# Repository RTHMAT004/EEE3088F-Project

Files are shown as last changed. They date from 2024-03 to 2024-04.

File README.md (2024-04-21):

# EEE3088F-Project
Power and Sensing repository for the EEE3088F Project. Group 24: RTHMAT004 and CLRMAT005

This repository contains files for both the sensing and power subsystems of a Micromouse for a university project. This project involved developing a Micromouse, therefore these solutions are built with existing systems in mind (microcontroller, servo motors etc). 

The power system deals with powering the two motors of the Micromouse, managing the charging of the battery and turning the Micromouse on and off.

The sensing system deals with surface detection around the Micromouse, inevitabely helping the micromouse navigate. The sensor does not make decisions of movement, or deal with any power control, it's only purpose is to detect objects and returning results using a voltage output signal. 

# Sensing subsystem:
The folder named "SensorKiCad-RTHMAT004" contains the KiCad files for the sensor subsystem. This subsystem solves the problem of sensing for the micromouse. This subsystem uses IR frequencies to detect objects within the bounds of the sensor. This subsystem solution should be used as a springboard for ideas surrounding sensing for devices such as a micromouse.  

# Power Subsytem
The folder named "PowerKiCad-CLRMAT005" contains the KiCad files for the power subsystem. This subsystem manages everything involving the powering of the Micromouse. This subsystem uses integrated circuits to control the motors and charging of the mouse. This subsystem solution should be used as a springboard for ideas surrounding the powering of small robotics.

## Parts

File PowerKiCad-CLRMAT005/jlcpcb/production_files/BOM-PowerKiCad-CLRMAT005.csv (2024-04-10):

Comment | Designator | Footprint | LCSC
0.1uF | C1,C2 | C_0603_1608Metric | C14663
1.2k | R3 | R_0805_2012Metric | C17379
470 | R2 | R_0805_2012Metric | C17710
4.7uF | C3,C4 | C_0805_2012Metric | C1779
SW_SPDT | SW1 | SW_Lever_1P2T_NKK_GW12LxH | C1788490
LED | D1 | LED_0603_1608Metric | C2286
LEFT MOTOR | U1,U2 | WSON-8-1EP_2x2mm_P0.5mm_EP0.9x1.6mm | C39159
2k | R1 | R_0402_1005Metric | C4109
3k | R4 | R_0603_1608Metric | C4211
MCP73831-2-OT | U3 | SOT-23-5 | C424093
Conn_01x02_Pin | J2 | JST_PH_B2B-PH-K_1x02_P2.00mm_Vertical
Conn_01x16_Pin | J1 | PinSocket_2x08_P2.54mm_Vertical

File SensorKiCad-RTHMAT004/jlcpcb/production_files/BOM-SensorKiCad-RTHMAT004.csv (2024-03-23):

Comment | Designator | Footprint | LCSC
BPV22NF | D10,D2,D3,D4 | XDCR_BPV22NF | C130226
47 | R1,R10,R12,R15,R17,R2,R20,R22,R25,R27,R30,R43,R47,R51,R55,R7 | R_0805_2012Metric | C17714
8.2k | R13,R18,R23,R28,R4,R40,R44,R48,R52,R8 | R_0805_2012Metric | C17828
100 | R11,R16,R21,R26,R3,R31,R32,R33,R34,R36,R38,R42,R46,R50,R54,R6 | R_0805_2012Metric | C17901
10k | R14,R19,R24,R29,R41,R5,R53,R9 | R_1206_3216Metric | C17902
SS8050 | Q1,Q2,Q3,Q4,Q5,Q6,Q7 | SOT-23 | C2150
SFH_4544 | D1,D5,D6,D7,D8,D9 | LED_D5.0mm_Horizontal_O1.27mm_Z3.0mm_IRBlack_JLCPCB | C2900370
1k | R35,R37,R39 | R_1206_3216Metric | C4410

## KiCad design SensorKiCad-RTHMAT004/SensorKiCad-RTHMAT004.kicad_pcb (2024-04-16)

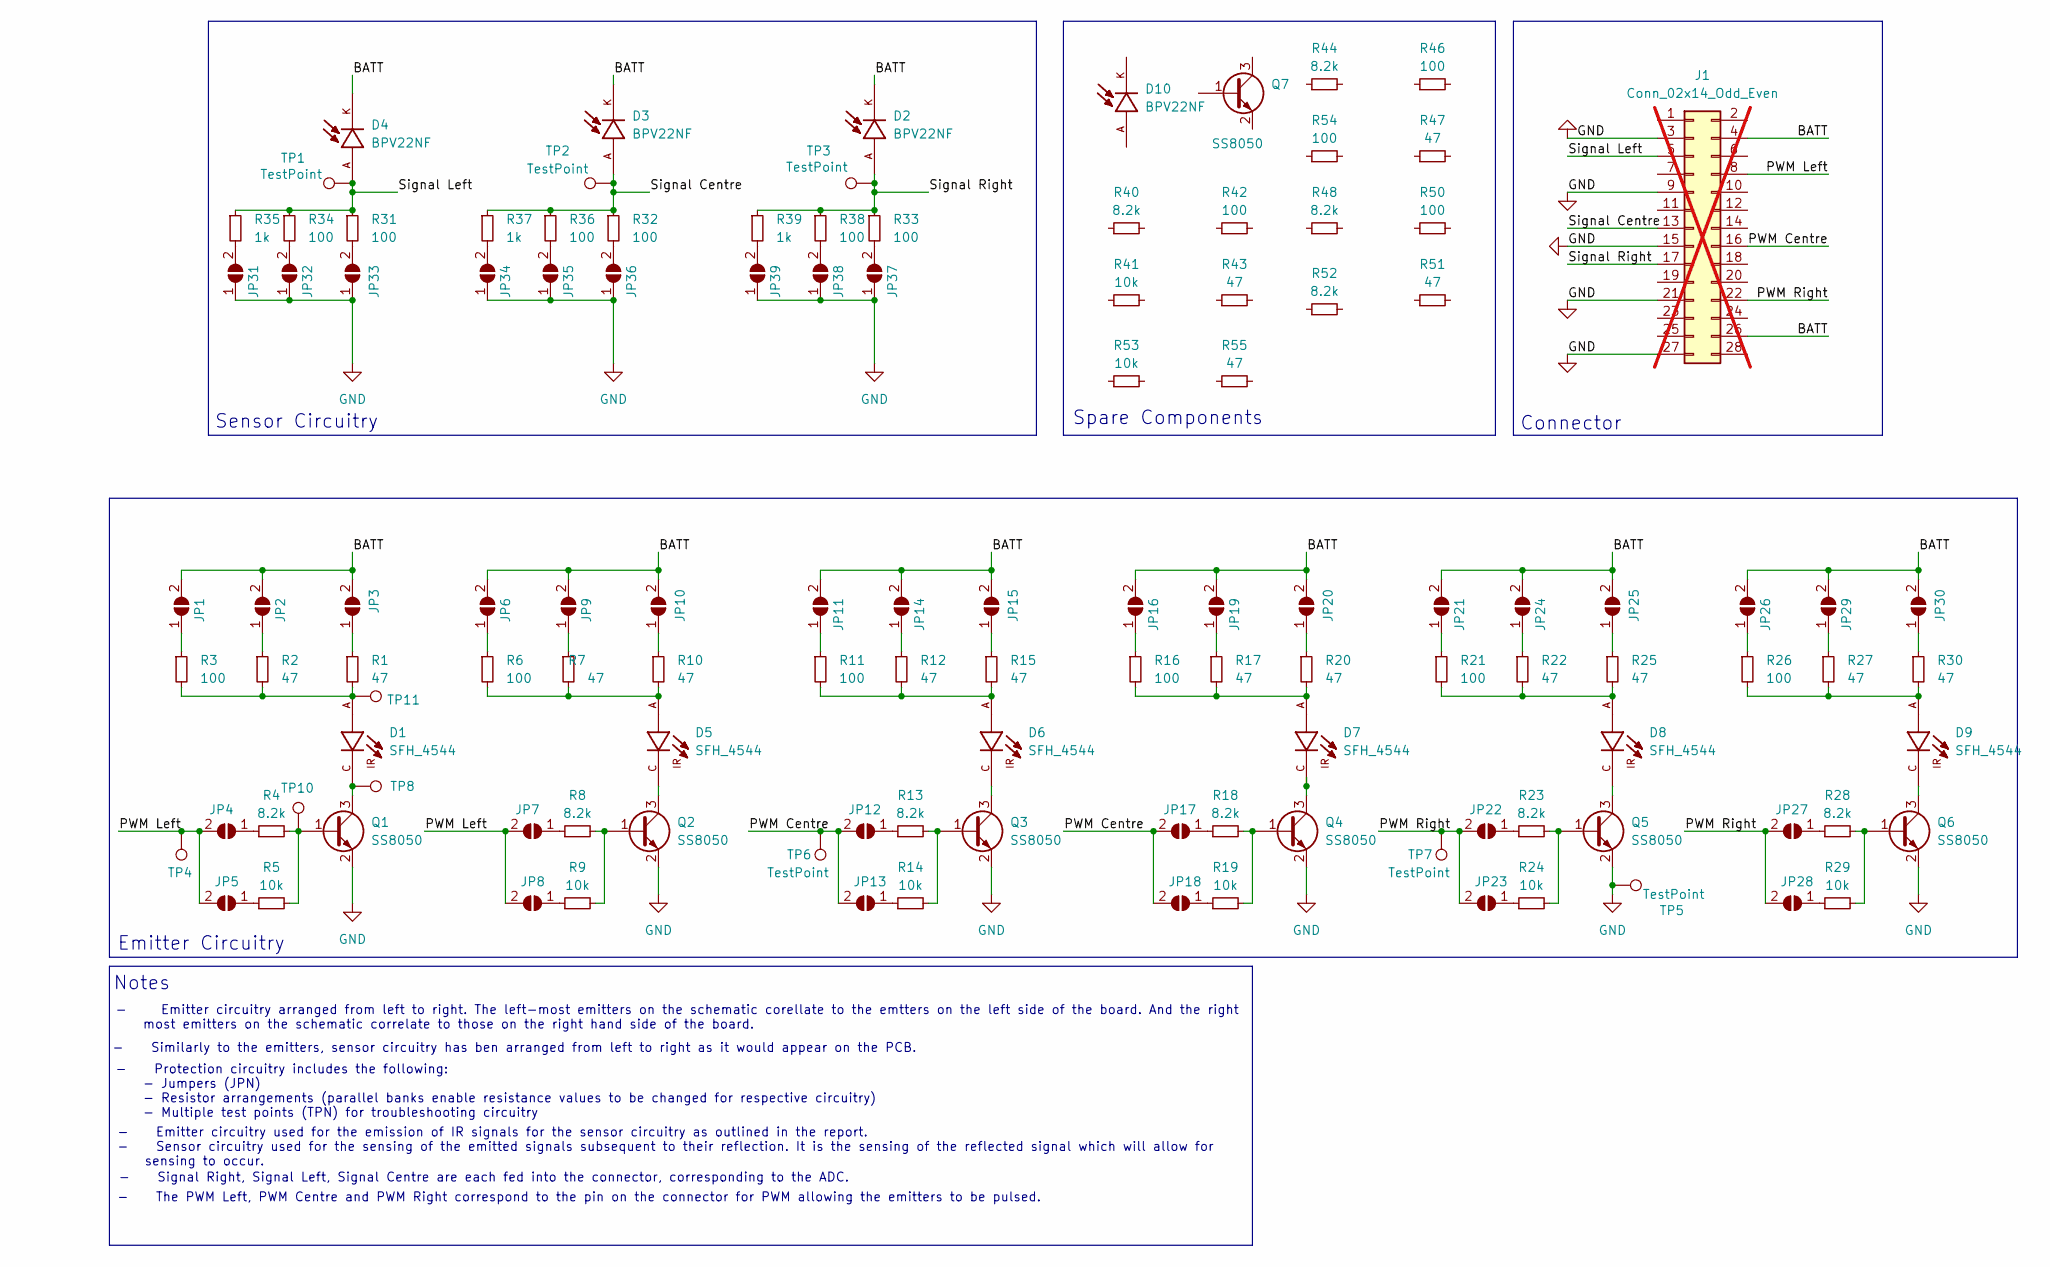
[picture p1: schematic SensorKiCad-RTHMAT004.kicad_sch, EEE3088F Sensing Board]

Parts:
D1, D5, D6, D7, D8, D9: SFH_4544; LED_D5.0mm_Horizontal_O1.27mm_Z3.0mm_IRBlack_JLCPCB; PARTREV 1.3; LCSC C2900370
D2, D3, D4, D10: BPV22NF; XDCR_BPV22NF; PARTREV 1.9; LCSC C130226
J1: Conn_02x14_Odd_Even; PinHeader_2x14_P2.54mm_Vertical; not fitted
JP1, JP2, JP3, JP4, JP5, JP6, JP7, JP8, JP9, JP10, JP11, JP12, JP13, JP14, JP15, JP16, JP17, JP18, JP19, JP20, JP21, JP22, JP23, JP24, JP25, JP26, JP27, JP28, JP29, JP30, JP31, JP32, JP33, JP34, JP35, JP36, JP37, JP38, JP39: SolderJumper_2_Open; SolderJumper-2_P1.3mm_Open_Pad1.0x1.5mm
Q1, Q2, Q3, Q4, Q5, Q6, Q7: SS8050; SOT-23; LCSC C2150
R1, R2, R7, R10, R12, R15, R17, R20, R22, R25, R27, R30, R43, R47, R51, R55: 47; R_0805_2012Metric; LCSC C17714
R3, R6, R11, R16, R21, R26, R31, R32, R33, R34, R36, R38, R42, R46, R50, R54: 100; R_0805_2012Metric; LCSC C17901
R4, R8, R13, R18, R23, R28, R40, R44, R48, R52: 8.2k; R_0805_2012Metric; LCSC C17828
R5, R9, R14, R19, R24, R29, R41, R53: 10k; R_1206_3216Metric; LCSC C17902
R35, R37, R39: 1k; R_1206_3216Metric; LCSC C4410
TP1, TP2, TP3, TP4, TP5, TP6, TP7, TP8, TP10, TP11: TestPoint; TestPoint_Pad_D2.5mm

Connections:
/3V3: J1.2
/BATT: D2.K, D3.K, D4.K, J1.4, J1.26, JP1.2 (B), JP2.2 (B), JP3.2 (B), JP6.2 (B), JP9.2 (B), JP10.2 (B), JP11.2 (B), JP14.2 (B), JP15.2 (B), JP16.2 (B), JP19.2 (B), JP20.2 (B), JP21.2 (B), JP24.2 (B), JP25.2 (B), JP26.2 (B), JP29.2 (B), JP30.2 (B)
/PWM Centre: J1.16, JP12.2 (B), JP13.2 (B), JP17.2 (B), JP18.2 (B), TP6.1
/PWM Left: J1.8, JP4.2 (B), JP5.2 (B), JP7.2 (B), JP8.2 (B), TP4.1
/PWM Right: J1.22, JP22.2 (B), JP23.2 (B), JP27.2 (B), JP28.2 (B), TP7.1
/Signal Centre: D3.A, J1.13, R32.1, R36.1, R37.1, TP2.1
/Signal Left: D4.A, J1.5, R31.1, R34.1, R35.1, TP1.1
/Signal Right: D2.A, J1.17, R33.1, R38.1, R39.1, TP3.1
GND: J1.3, J1.9, J1.15, J1.21, J1.27, JP31.1 (A), JP32.1 (A), JP33.1 (A), JP34.1 (A), JP35.1 (A), JP36.1 (A), JP37.1 (A), JP38.1 (A), JP39.1 (A), Q1.2 (E), Q2.2 (E), Q3.2 (E), Q4.2 (E), Q5.2 (E), Q6.2 (E), TP5.1
unnamed: D1.A, R1.2, R2.2, R3.2, TP11.1
unnamed: D5.A, R6.2, R7.2, R10.2
unnamed: D6.A, R11.2, R12.2, R15.2
unnamed: D7.A, R16.2, R17.2, R20.2
unnamed: D8.A, R21.2, R22.2, R25.2
unnamed: D9.A, R26.2, R27.2, R30.2
unnamed: JP1.1 (A), R3.1
unnamed: JP2.1 (A), R2.1
unnamed: JP3.1 (A), R1.1
unnamed: JP4.1 (A), R4.1
unnamed: JP5.1 (A), R5.1
unnamed: JP6.1 (A), R6.1
unnamed: JP7.1 (A), R8.1
unnamed: JP8.1 (A), R9.1
unnamed: JP9.1 (A), R7.1
unnamed: JP10.1 (A), R10.1
unnamed: JP11.1 (A), R11.1
unnamed: JP12.1 (A), R13.1
unnamed: JP13.1 (A), R14.1
unnamed: JP14.1 (A), R12.1
unnamed: JP15.1 (A), R15.1
unnamed: JP16.1 (A), R16.1
unnamed: JP17.1 (A), R18.1
unnamed: JP18.1 (A), R19.1
unnamed: JP19.1 (A), R17.1
unnamed: JP20.1 (A), R20.1
unnamed: JP21.1 (A), R21.1
unnamed: JP22.1 (A), R23.1
unnamed: JP23.1 (A), R24.1
unnamed: JP24.1 (A), R22.1
unnamed: JP25.1 (A), R25.1
unnamed: JP26.1 (A), R26.1
unnamed: JP27.1 (A), R28.1
unnamed: JP28.1 (A), R29.1
unnamed: JP29.1 (A), R27.1
unnamed: JP30.1 (A), R30.1
unnamed: JP31.2 (B), R35.2
unnamed: JP32.2 (B), R34.2
unnamed: JP33.2 (B), R31.2
unnamed: JP34.2 (B), R37.2
unnamed: JP35.2 (B), R36.2
unnamed: JP36.2 (B), R32.2
unnamed: JP37.2 (B), R33.2
unnamed: JP38.2 (B), R38.2
unnamed: JP39.2 (B), R39.2
unnamed: Q1.1 (B), R4.2, R5.2, TP10.1
unnamed: D1.C, Q1.3 (C), TP8.1
unnamed: Q2.1 (B), R8.2, R9.2
unnamed: D5.C, Q2.3 (C)
unnamed: Q3.1 (B), R13.2, R14.2
unnamed: D6.C, Q3.3 (C)
unnamed: Q4.1 (B), R18.2, R19.2
unnamed: D7.C, Q4.3 (C)
unnamed: Q5.1 (B), R23.2, R24.2
unnamed: D8.C, Q5.3 (C)
unnamed: Q6.1 (B), R28.2, R29.2
unnamed: D9.C, Q6.3 (C)

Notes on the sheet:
- Protection circuitry includes the following: - Jumpers (JPN) - Resistor arrangements (parallel banks enable resistance values to be changed for respective circuitry) - Multiple test points (TPN) for troubleshooting circuitry
Spare Components
Notes
- Emitter circuitry arranged from left to right. The left-most emitters on the schematic corellate to the emtters on the left side of the board. And the right most emitters on the schematic correlate to those on the right hand side of the board.
Emitter Circuitry
- Emitter circuitry used for the emission of IR signals for the sensor circuitry as outlined in the report. - Sensor circuitry used for the sensing of the emitted signals subsequent to their reflection. It is the sensing of the reflected signal which will allow for sensing to occur.
Sensor Circuitry
- The PWM Left, PWM Centre and PWM Right correspond to the pin on the connector for PWM allowing the emitters to be pulsed.
- Similarly to the emitters, sensor circuitry has ben arranged from left to right as it would appear on the PCB.
Connector
- Signal Right, Signal Left, Signal Centre are each fed into the connector, corresponding to the ADC.

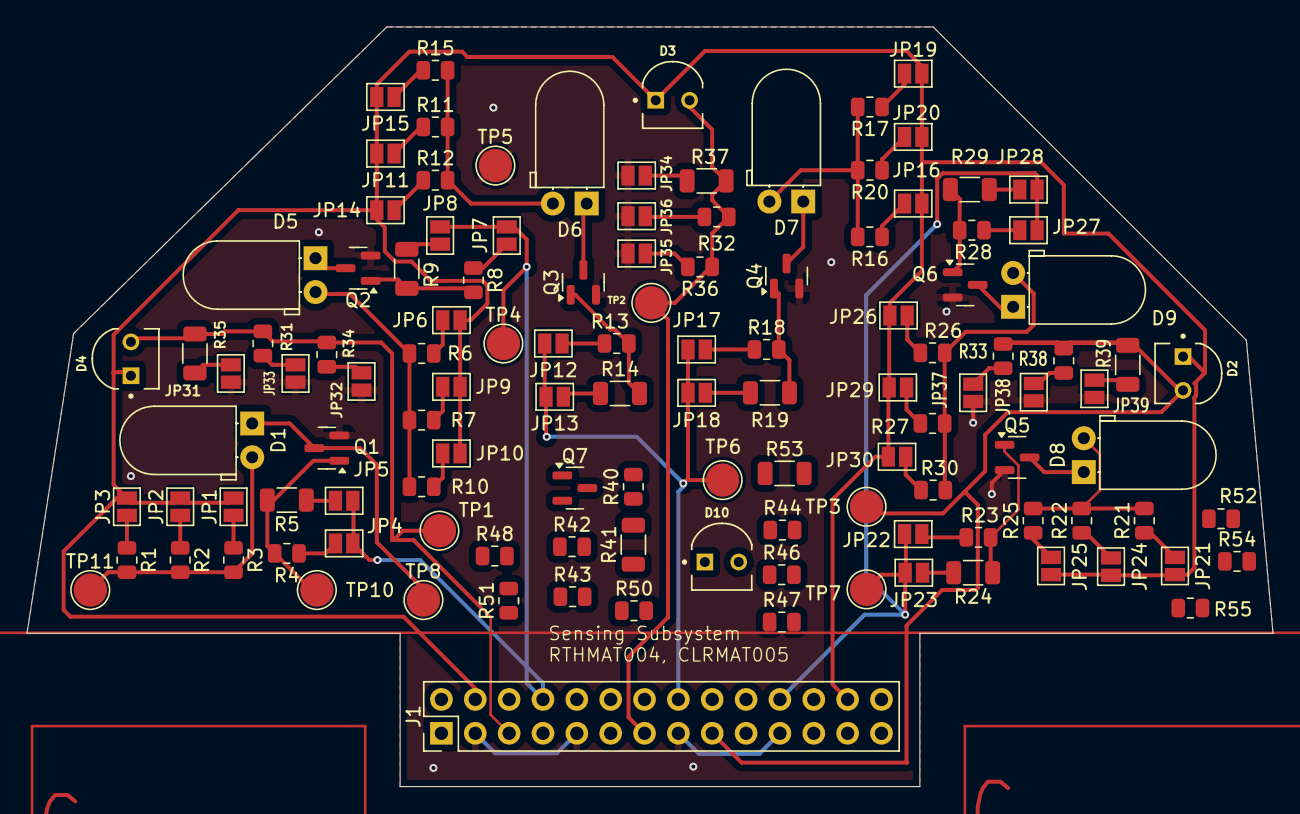
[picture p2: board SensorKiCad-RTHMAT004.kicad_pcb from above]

Board: 2 copper layers, 93.5 x 57.0 mm, 120 parts (0 on the bottom side), 65 nets.

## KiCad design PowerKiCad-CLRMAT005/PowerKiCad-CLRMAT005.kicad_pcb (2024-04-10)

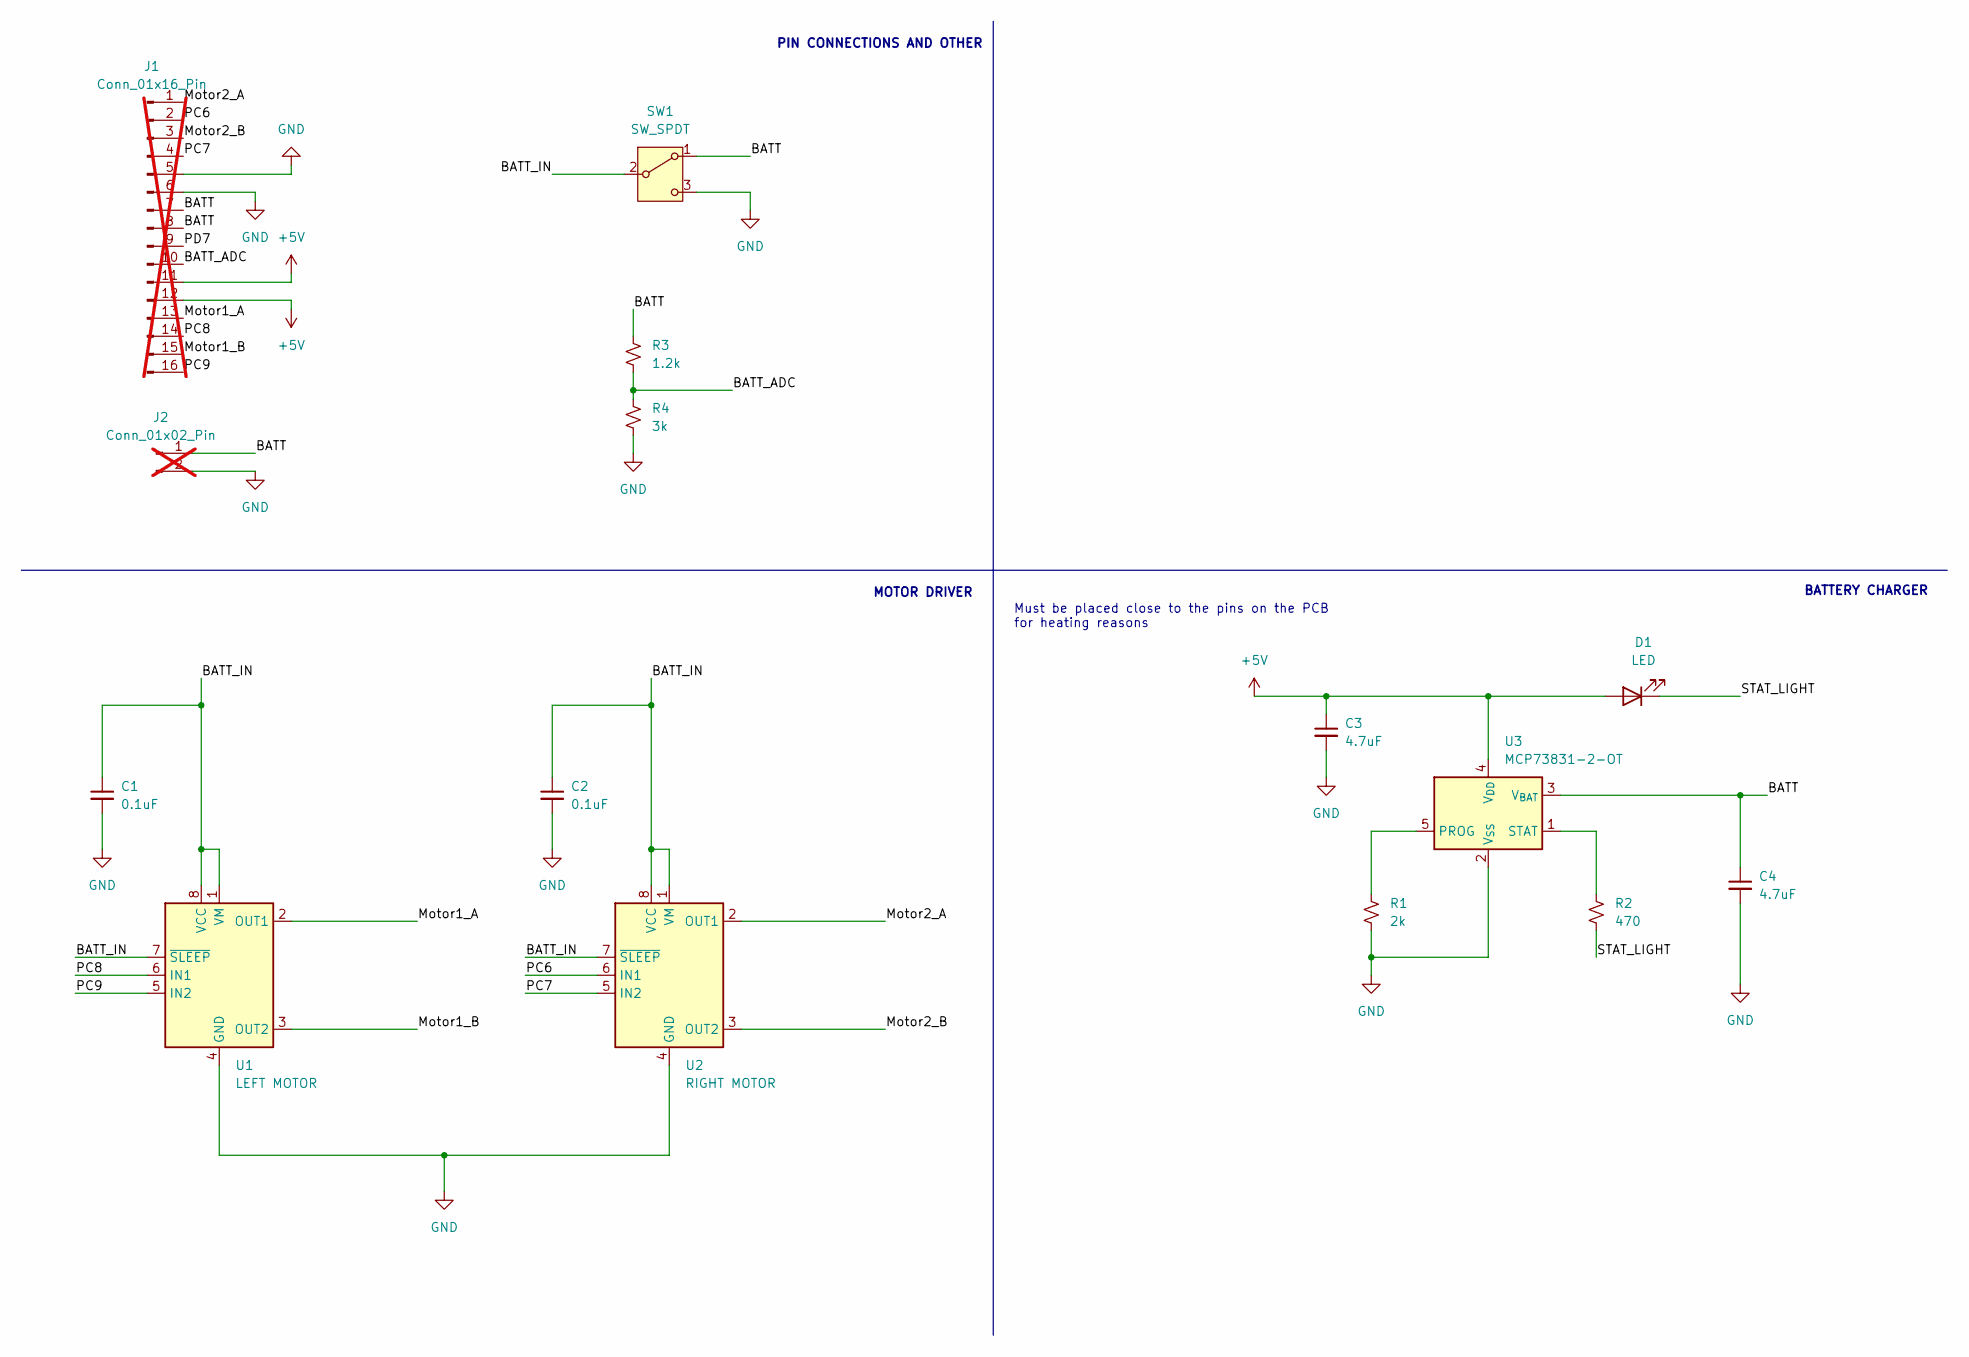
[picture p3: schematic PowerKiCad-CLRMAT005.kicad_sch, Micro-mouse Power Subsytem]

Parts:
C1, C2: 0.1uF; C_0603_1608Metric
C3, C4: 4.7uF; C_0805_2012Metric
D1: LED; LED_0603_1608Metric
J1: Conn_01x16_Pin; PinSocket_2x08_P2.54mm_Vertical; not fitted
J2: Conn_01x02_Pin; JST_PH_B2B-PH-K_1x02_P2.00mm_Vertical; not fitted
R1: 2k; R_0402_1005Metric
R2: 470; R_0805_2012Metric
R3: 1.2k; R_0805_2012Metric
R4: 3k; R_0603_1608Metric
SW1: SW_SPDT; SW_Lever_1P2T_NKK_GW12LxH
U1: LEFT MOTOR; WSON-8-1EP_2x2mm_P0.5mm_EP0.9x1.6mm
U2: RIGHT MOTOR; WSON-8-1EP_2x2mm_P0.5mm_EP0.9x1.6mm
U3: MCP73831-2-OT; SOT-23-5

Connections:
+5V: C3.1, D1.2 (A), J1.11, J1.12, U3.4 (V_{DD})
/BATT: C4.1, J1.7, J1.8, J2.1, R3.1, SW1.1 (A), U3.3 (V_{BAT})
/BATT_ADC: J1.10, R3.2, R4.1
/BATT_IN: C1.1, C2.1, SW1.2 (B), U1.1 (VM), U1.7 (~SLEEP), U1.8 (VCC), U2.1 (VM), U2.7 (~SLEEP), U2.8 (VCC)
/Motor1_A: J1.13, U1.2 (OUT1)
/Motor1_B: J1.15, U1.3 (OUT2)
/Motor2_A: J1.1, U2.2 (OUT1)
/Motor2_B: J1.3, U2.3 (OUT2)
/PC6: J1.2, U2.6 (IN1)
/PC7: J1.4, U2.5 (IN2)
/PC8: J1.14, U1.6 (IN1)
/PC9: J1.16, U1.5 (IN2)
/PD7: J1.9
/STAT_LIGHT: D1.1 (K), R2.2
GND: C1.2, C2.2, C3.2, C4.2, J1.5, J1.6, J2.2, R1.2, R4.2, SW1.3 (C), U1.4 (GND), U1.9 (GND), U2.4 (GND), U2.9 (GND), U3.2 (V_{SS})
unnamed: R1.1, U3.5 (PROG)
unnamed: R2.1, U3.1 (STAT)

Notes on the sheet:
PIN CONNECTIONS AND OTHER
BATTERY CHARGER
for heating reasons
Must be placed close to the pins on the PCB
MOTOR DRIVER

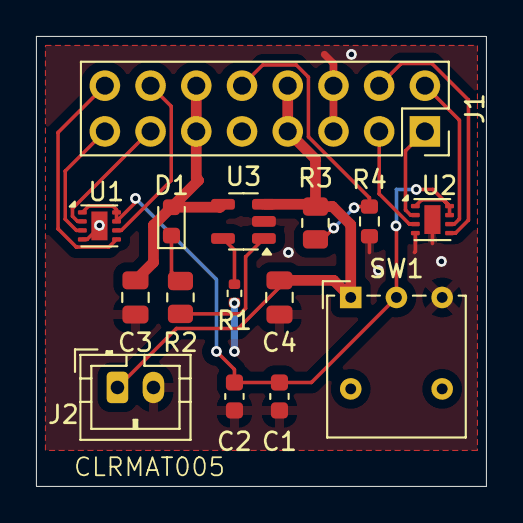
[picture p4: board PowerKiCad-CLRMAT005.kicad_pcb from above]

Board: 2 copper layers, 25.0 x 25.0 mm, 15 parts (0 on the bottom side), 16 nets.

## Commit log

2024-03-16 Sensor KiCad
    [SensorKiCad-RTHMAT004.kicad_pcb, SensorKiCad-RTHMAT004.kicad_sch]
2024-03-16 This is my Power KiCad Project
    [PowerKiCad-CLRMAT005.kicad_pcb, PowerKiCad-CLRMAT005.kicad_sch]
2024-03-16 Unpopulated pins
    [SensorKiCad-RTHMAT004.kicad_sch]
2024-03-17 Small changes to Sensor KiCAD file
    [SensorKiCad-RTHMAT004.kicad_sch]
2024-03-21 Finalising PCB
    [BOM-SensorKiCad-RTHMAT004.csv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]
2024-03-21 pcb advancements
    [BOM-SensorKiCad-RTHMAT004.csv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]
2024-03-23 Final changes to sensor
    [BOM-SensorKiCad-RTHMAT004.csv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]
2024-04-10 Finalised KiCad files =
    [BOM-PowerKiCad-CLRMAT005.csv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]
2024-04-16 Final changes to git repo
    [SensorKiCad-RTHMAT004.kicad_pcb, SensorKiCad-RTHMAT004.kicad_sch]
2024-04-16 added stuff to power subfolder
    [PowerKiCad-CLRMAT005.kicad_sch]
